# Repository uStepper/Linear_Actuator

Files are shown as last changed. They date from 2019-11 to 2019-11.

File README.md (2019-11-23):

# Linear_Actuator
This repository contains the files for the uStepper Linear Actuator - both M8 and T8x8 version. 
See more here: https://ustepper.com/store/kits/43-80-ustepper-linear-actuator.html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

<br /><span xmlns:dct="http://purl.org/dc/terms/" property="dct:title">uStepper & uStepper Linear Actuator</span> by <a xmlns:cc="http://creativecommons.org/ns#" href="www.ustepper.com" property="cc:attributionName" rel="cc:attributionURL">ON Development</a> is licensed under a <a rel="license" href="http://creativecommons.org/licenses/by-nc-sa/4.0/">Creative Commons Attribution-NonCommercial-ShareAlike 4.0 International License</a>.

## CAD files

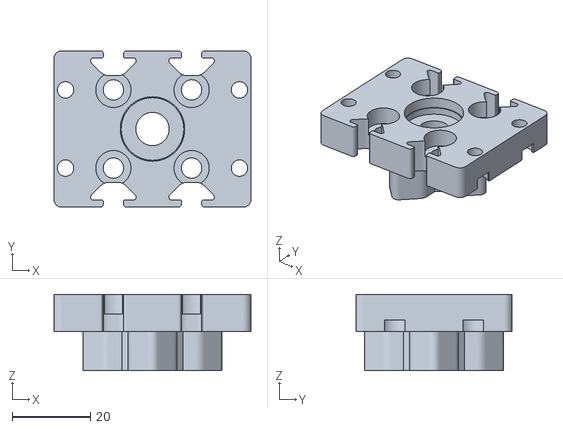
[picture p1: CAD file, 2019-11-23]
M8/STL/2-Bearingcap.stl
50.4 x 40.0 x 19.5

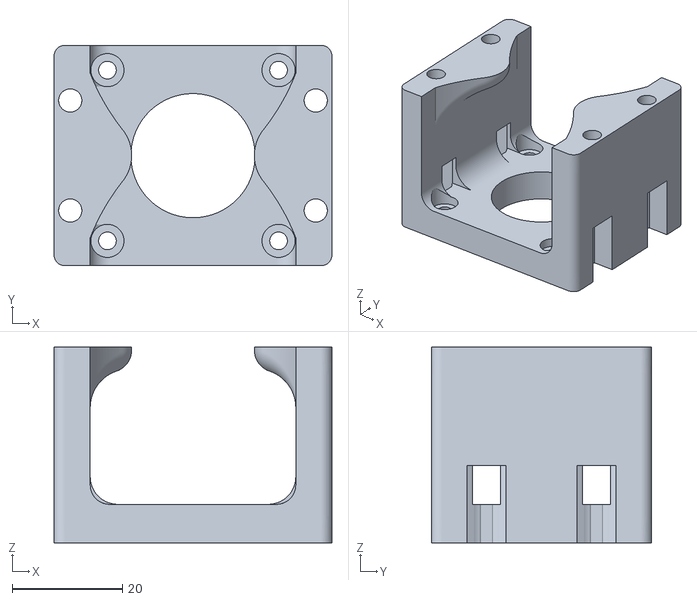
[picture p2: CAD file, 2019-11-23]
T8x8/STL/3-Motor_bracket.stl
50.4 x 40.0 x 35.5

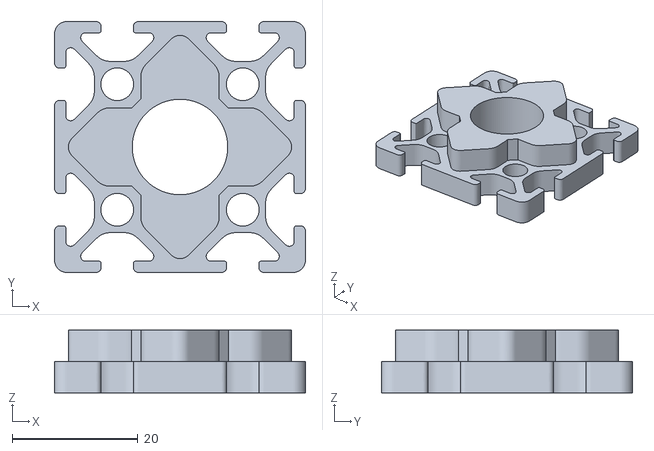
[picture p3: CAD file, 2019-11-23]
M8/STL/4-Endcap.stl
40.0 x 40.0 x 10.0

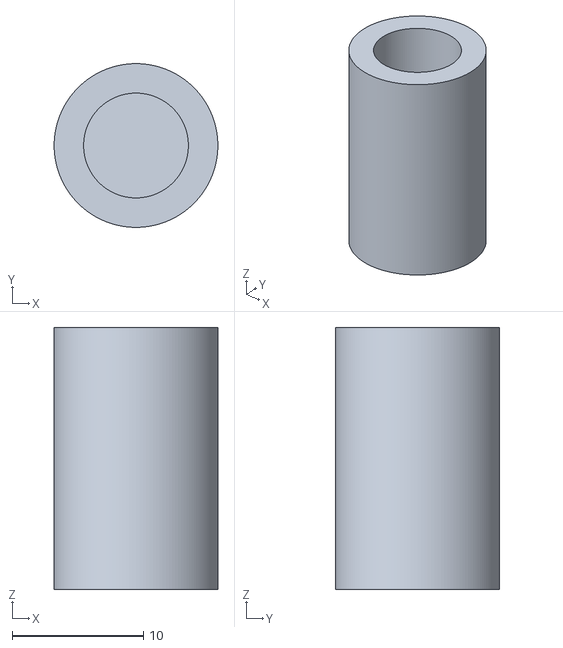
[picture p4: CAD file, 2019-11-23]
T8x8/STL/5-Rod_endcap.stl
12.5 x 12.5 x 20.0

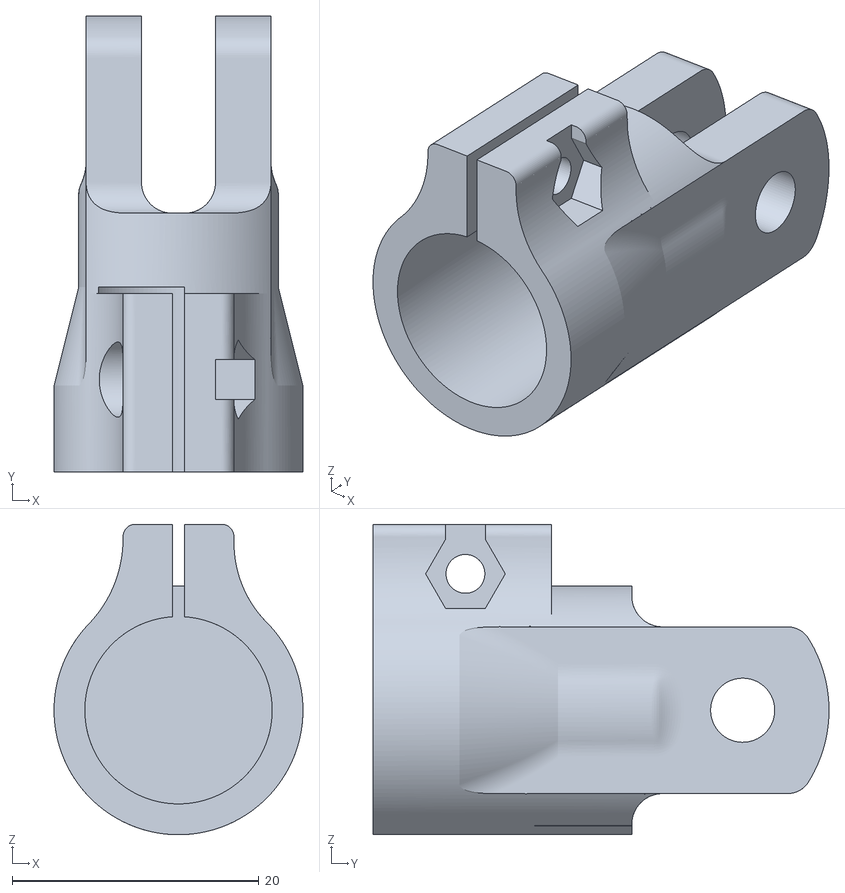
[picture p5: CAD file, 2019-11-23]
M8/STL/6-Rod_end.stl
20.2 x 37.0 x 25.2

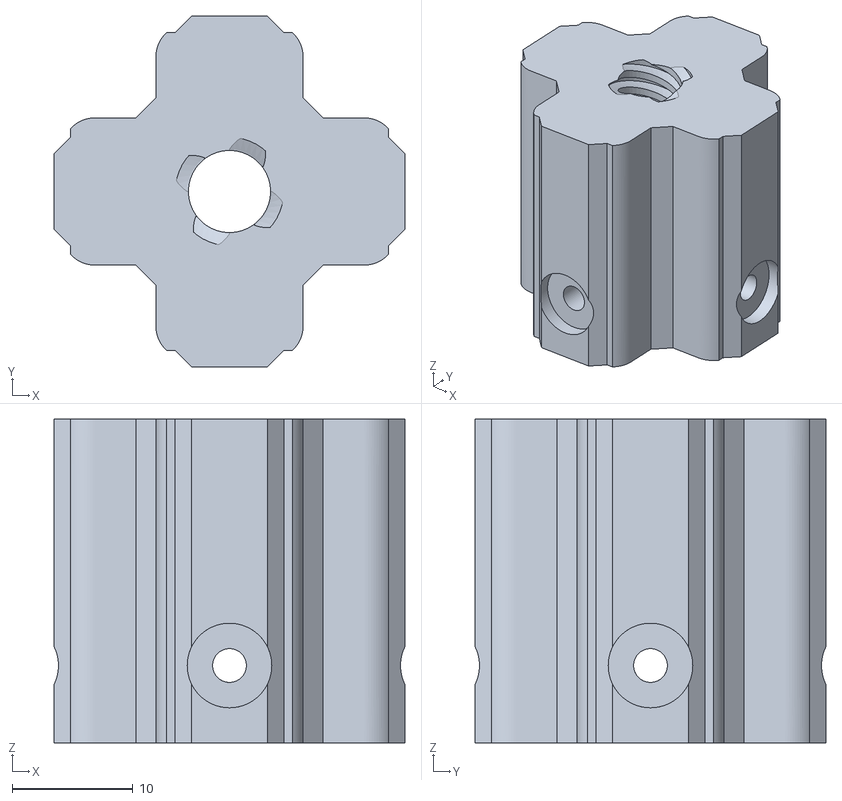
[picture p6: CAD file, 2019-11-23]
T8x8/STL/1-T8_nut.stl
29.1 x 29.1 x 26.8

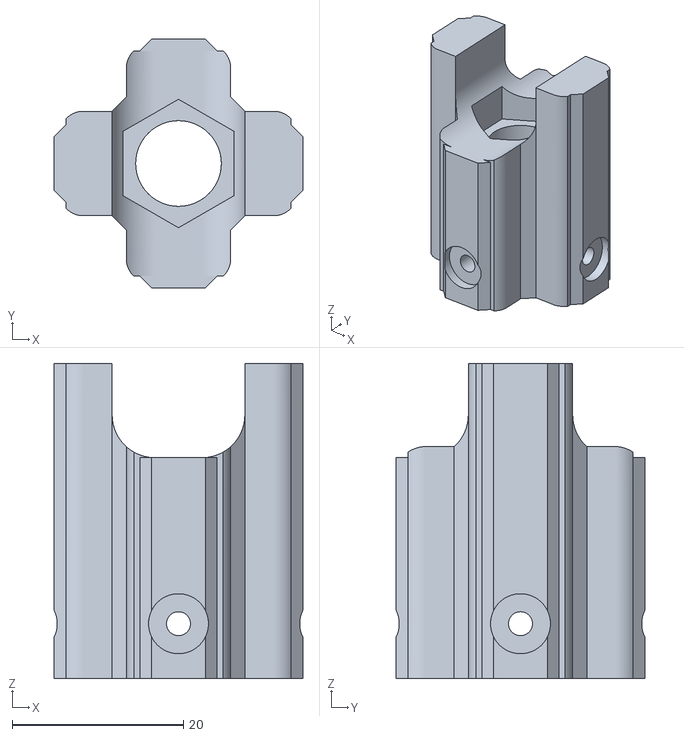
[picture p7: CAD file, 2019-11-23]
M8/STL/1-M8_nut.stl
29.1 x 29.1 x 36.8

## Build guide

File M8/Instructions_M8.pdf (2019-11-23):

# uStepper Linear Actuator

## M8 lead screw

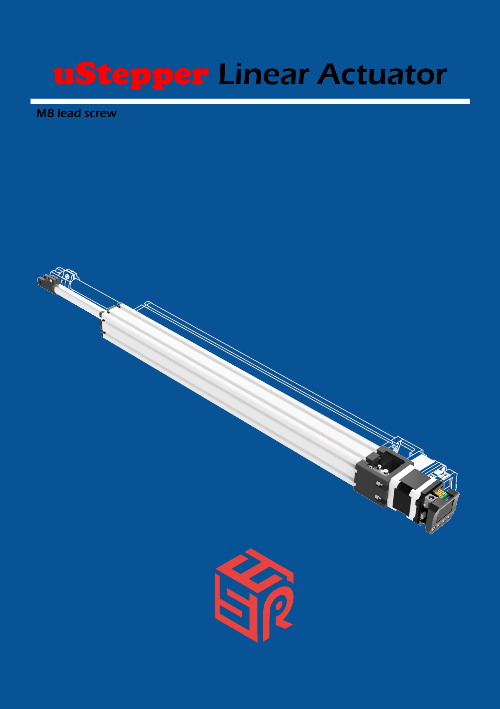
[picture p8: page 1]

# Introduction

## This document describes the assembly and use of uStepper Linear Actuator

and related products.

# Product: uStepper Linear Actuator M8

## Document revision: 1.0

## Author: MGN

## Approved by: THO

## Approval date: November 19th 2019

1

### 1 x

2

### 1 x

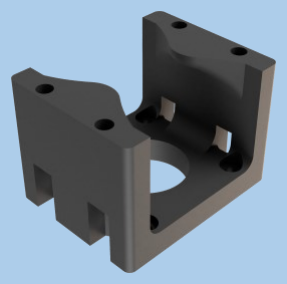
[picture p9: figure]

3

### 1 x

4

### 1 x

5

### 1 x

# Bill Of Materials

6

### 1 x

### 4 x M4 x 35 mm

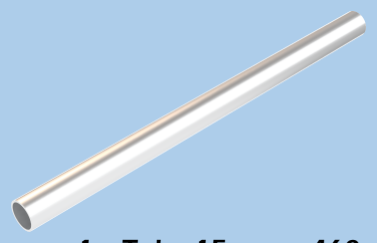
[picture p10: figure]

### 1 x Tube 15 mm x 460 mm

### 8 x M5 x 20 mm

### 2 x M8 nut

### 4 x M4 SL nut

### 1 x M8 SL nut

### 2 x F8-16M Bearing

# Bill Of Materials

### 3 x M3 x 10 mm

### 1 x M3 SL nut

### 1 x M8 lead screw x 470 mm

### 1 x 40x40 I-type slot 5, 450 mm

### 4 x 3.5x8 mm screw

### 1 x M8x5 coupler

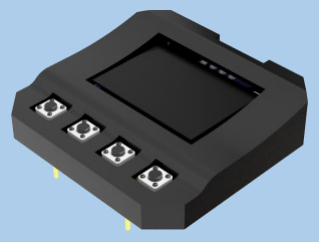
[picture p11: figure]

### 1 x uStepper Ego Shield S

### 1 x uStepper S w. motor

### 4 x M3 x 6 mm

# Linear Actuator Assembly

1x | 1x | 2x

1

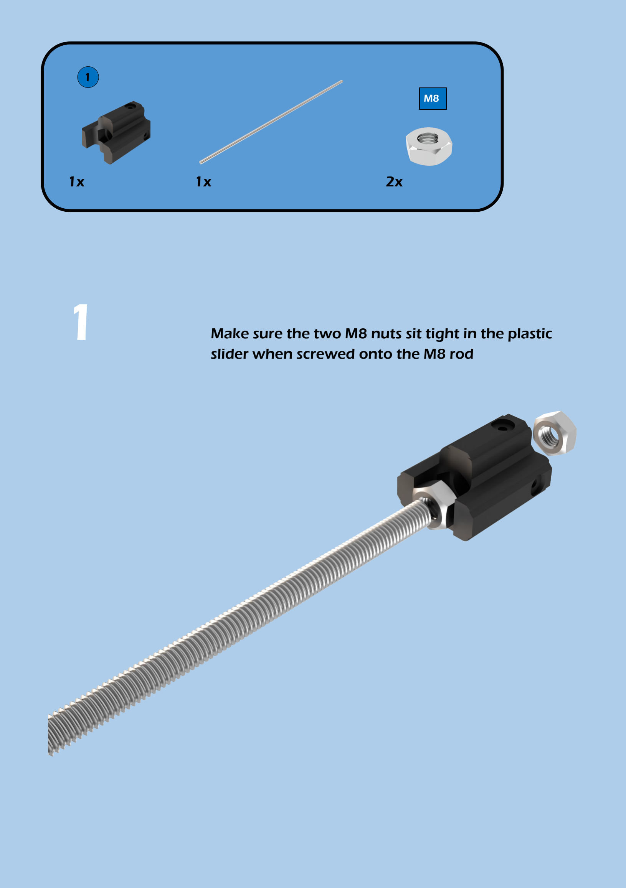
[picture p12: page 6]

1

M8

## Make sure the two M8 nuts sit tight in the plastic slider when screwed onto the M8 rod

1x | 2x | 1x | 4x | 1x

2

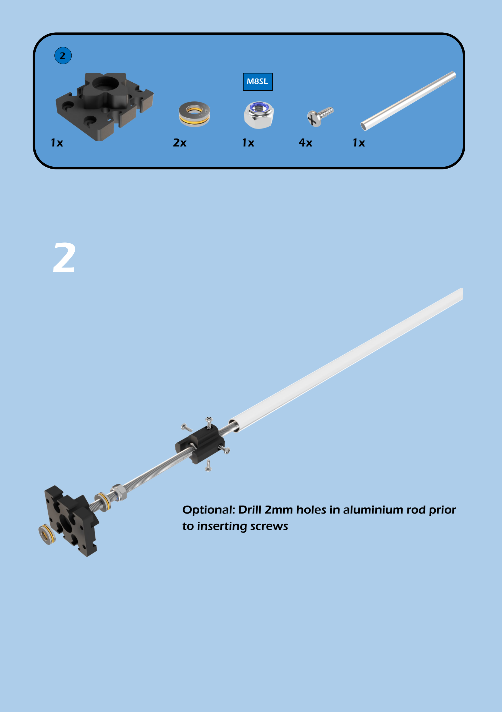
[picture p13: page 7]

2

M8SL

## Optional: Drill 2mm holes in aluminium rod prior to inserting screws

3

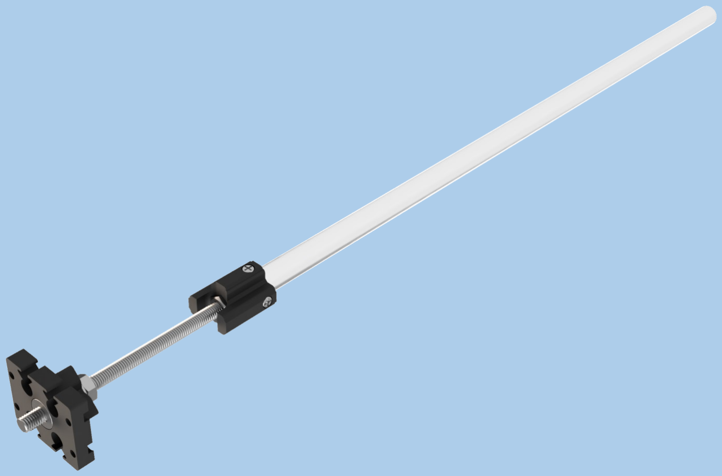
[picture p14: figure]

1x

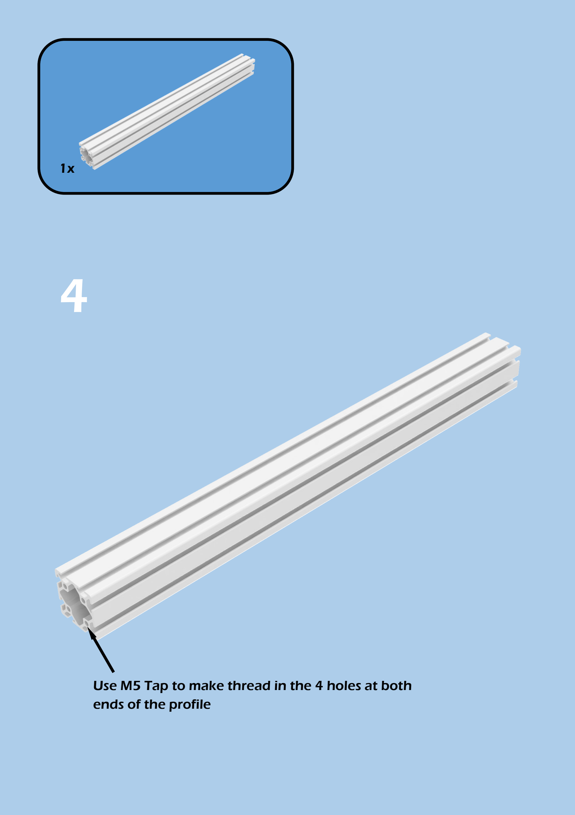
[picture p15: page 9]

4

## Use M5 Tap to make thread in the 4 holes at both ends of the profile

5

M5x20

4x

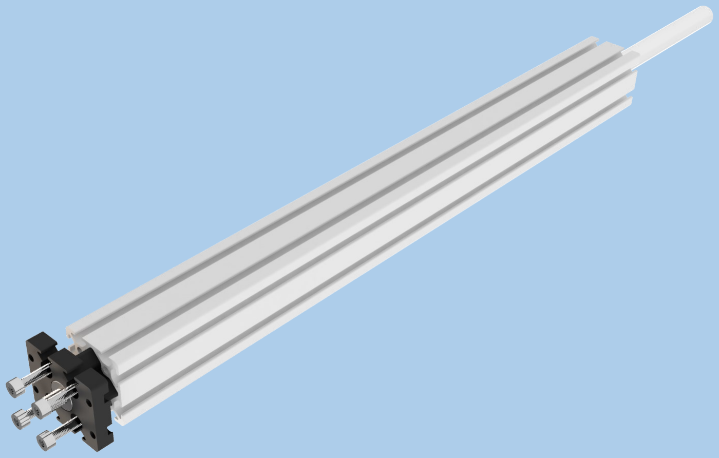
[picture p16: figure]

6

1x | 4x

M3x6

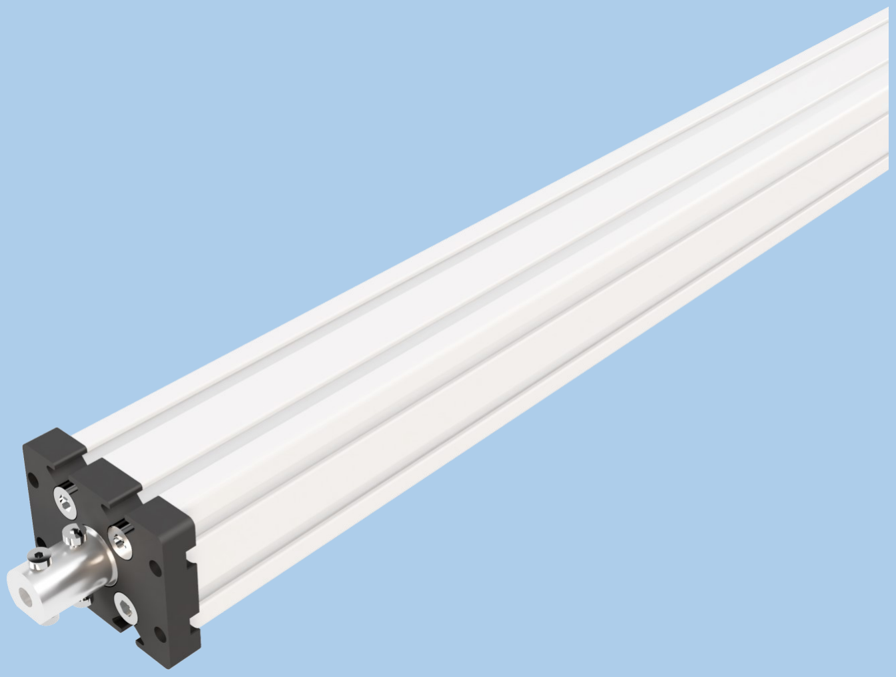
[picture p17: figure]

1x | 1x

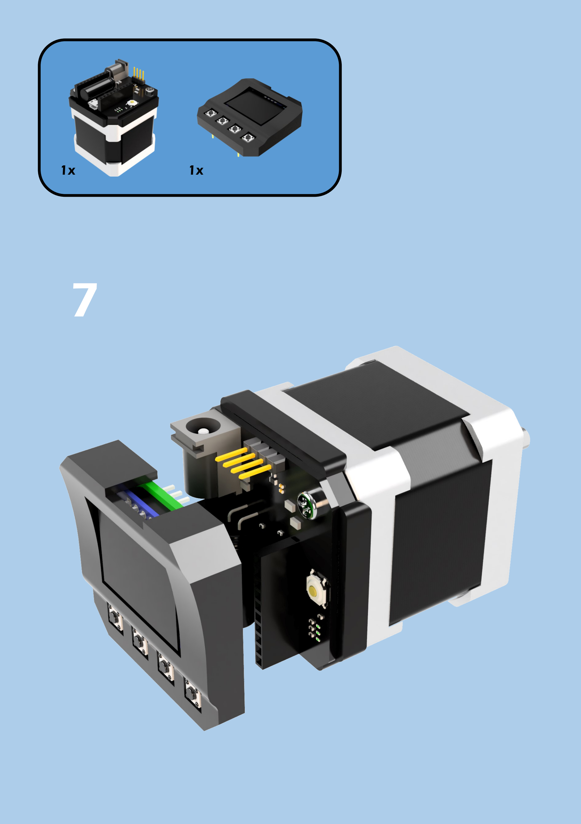
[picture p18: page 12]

7

1x | 2x

3

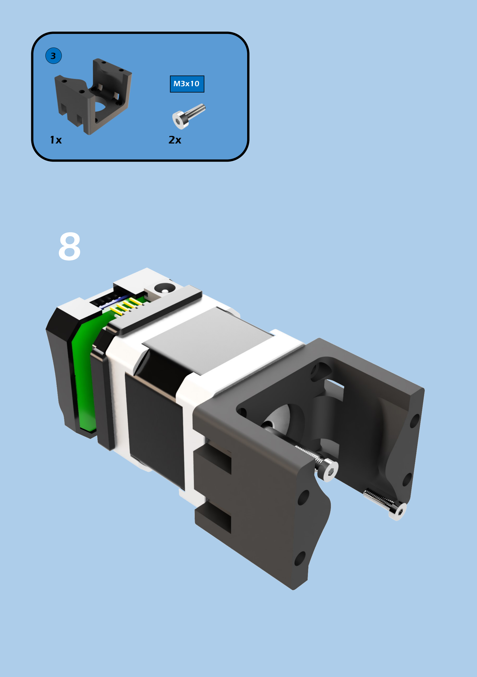
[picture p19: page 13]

8

M3x10

9

4x | 4x
M4x35 | M4SL

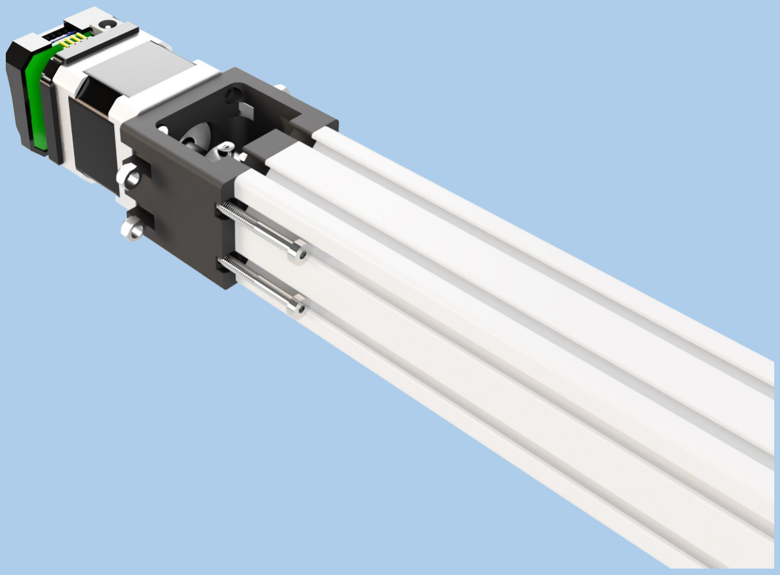
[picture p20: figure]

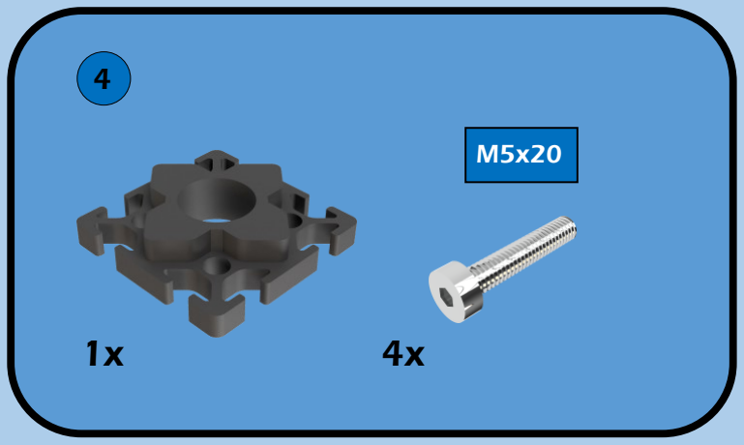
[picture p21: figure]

10

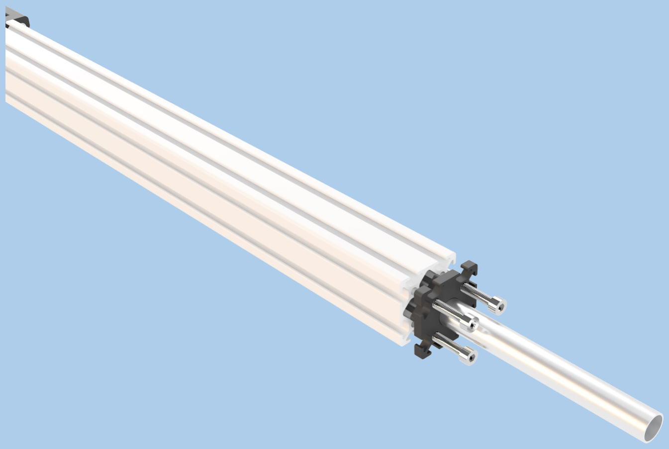
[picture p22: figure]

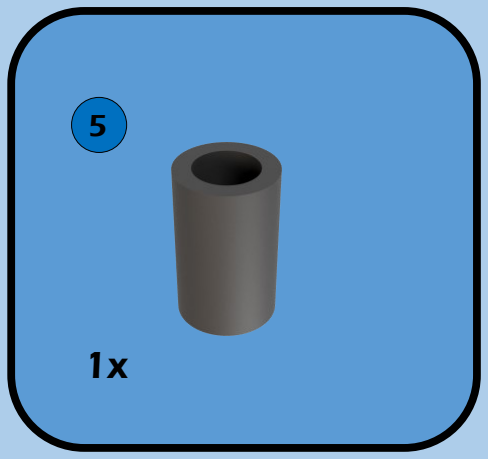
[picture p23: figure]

11

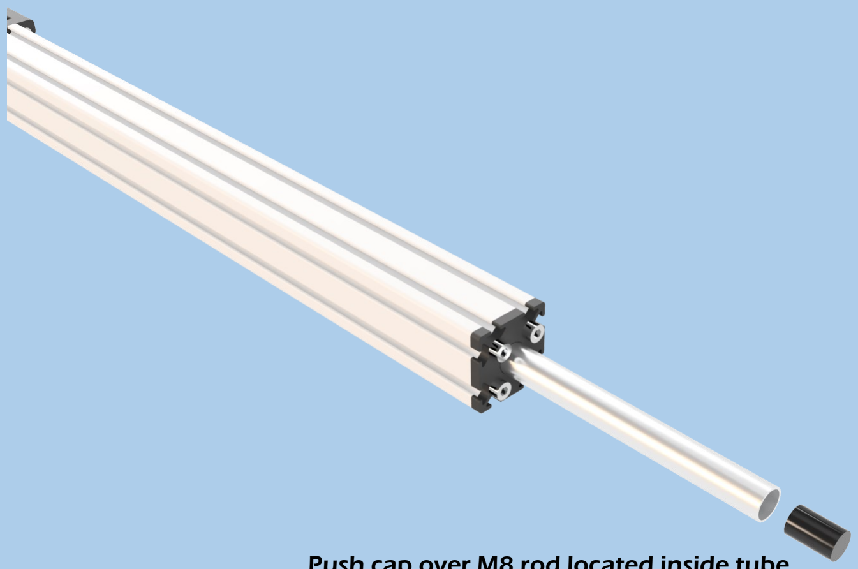
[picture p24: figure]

## Push cap over M8 rod located inside tube

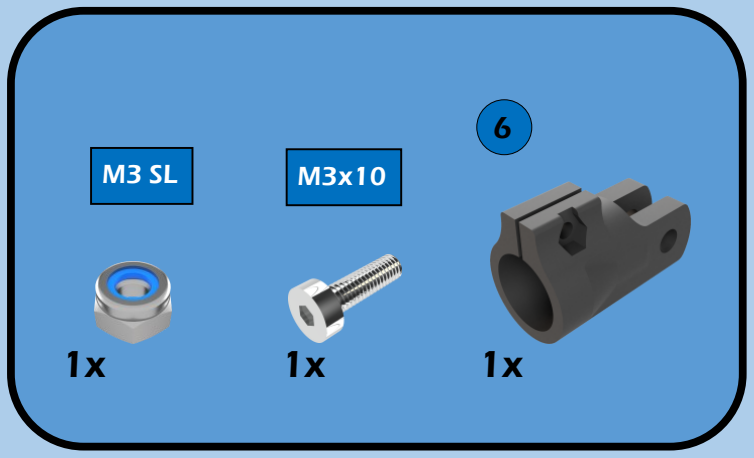
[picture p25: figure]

12

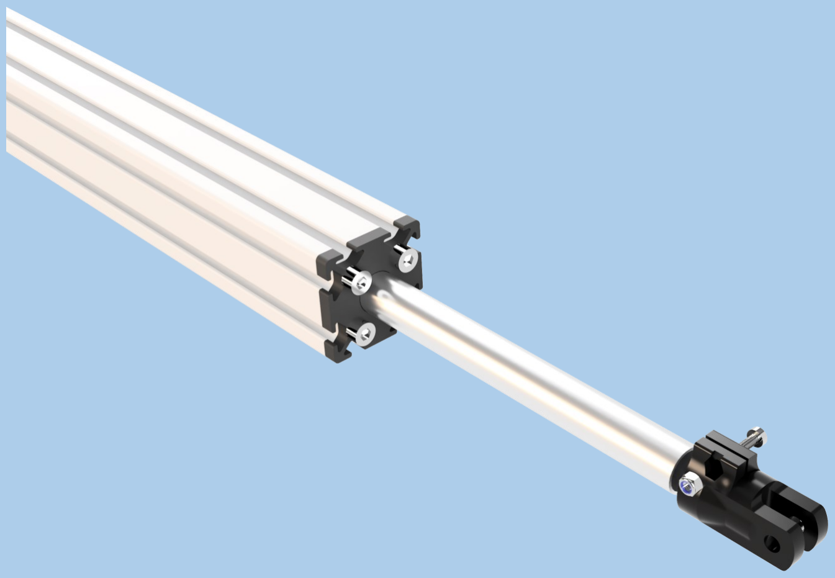
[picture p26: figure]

13

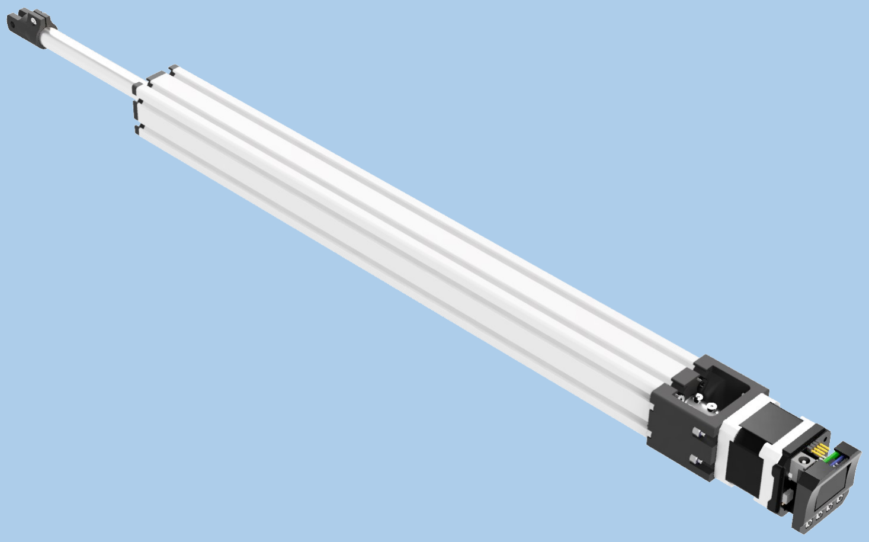
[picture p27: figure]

# Using uStepper & Ego Shield

To get started with using the linear actuator with uStepper S and Ego Shield S load the Ego Shield Teach

### example sketch and/or follow the instructions below !

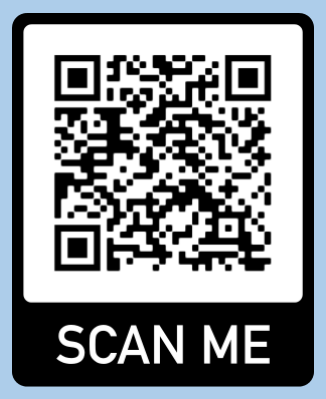
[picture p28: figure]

## Mounting uStepper

### To see how you mount uStepper S to your stepper motor correctly, please visit the

product sheet by pressing THIS LINK (https://ustepper.com/store/index.php?controller=attachment&id_attachment=9) or scanning the QR code here on the right !

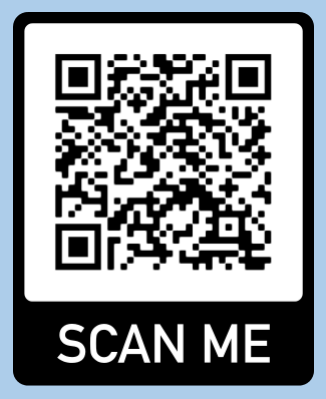
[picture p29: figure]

## Mounting and using Ego Shield

### To see how you mount the Ego Shield and what functionality comes with it please

visit the product sheet on THIS LINK (https://ustepper.com/store/index.php?controller=attachment&id_attachment=14) or scan the QR coder here on the right !

## Video Tutorials

On our YouTube channel you will find video tutorials on how to mount uStepper S, setting it up in the Arduino IDE and programming it. You will also find a tutorial for using the Ego Shield with the linear

### actuator !

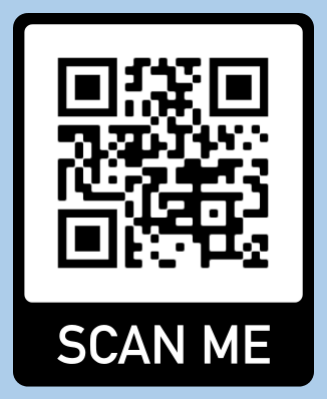
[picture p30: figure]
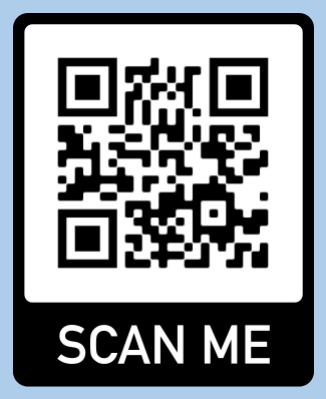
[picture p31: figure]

Mounting uStepper S (https://youtu.be/oYFnBv0kocI) | Programming uStepper S (https://youtu.be/V5M66Nhyn5s) | Using Ego Shield (https://youtu.be/wa8sdel2Xgg)

### For further info visit www.uStepper.com and our YouTube channel !

# Disclaimer

1 Disclaimers and Limitation of Liability

1.1 uStepper ApS and/or ON Development IVS (or any individuals affiliated with either of the two companies) can not be held responsible for any damage inflicted upon mounting or interfacing with uStepper products This also includes damage to stepper motors (both electrical and mechanical) or any other 3rd party hardware connected to or interfacing with any uStepper products. Most stepper motor cases are made of aluminum, and care must be taken when preparing the mountings for uStepper.

1.2 uStepper ApS and/or ON Development IVS (or any individuals affiliated with either of the two companies) can not be held responsible for any damage inflicted upon assembly of the uStepper Robot Arm. This includes damage to 3D printed parts, which must be considered to be of prototyping quality compared to injection moulded parts. Care must be taken while assembling 3D printed parts, and use of excessive force may lead to damage of the parts.

1.3 By using the uStepper products (including, but not limited to, hardware and software) you acknowledge that uStepper ApS and/or ON Development IVS (or any individuals affiliated with either of the two companies) can not be held responsible for any personal injuries and/or damage to any 3rd party hardware that may occur when using the uStepper products.

1.4 To the extent permitted by law, uStepper ApS and/or ON Development IVS will not be liable for any indirect or consequential loss or damage, of any kind, (including without limitation loss of business, opportunity, data, profits) arising out of or in connection with the use of any products (including, but not limited to, hardware and software), developed, produced or sold by uStepper ApS and/or ON Development IVS (or any individuals affiliated with either of the two companies).

1.5 Nothing in these Terms and Conditions shall be construed so as to hold uStepper ApS and/or ON Development IVS liable for death or personal injury as a result of the negligence of uStepper ApS and/or ON Development IVS or that of its employees or agents.

2 Indemnity

2.1 You agree to indemnify and hold uStepper ApS and/or ON Development IVS and its employees and agents harmless from and against all liabilities, legal fees, damages, losses, costs and other expenses in relation to any claims or actions brought against uStepper ApS and/or ON Development IVS arising out of any breach by you of these Terms and Conditions or other liabilities arising out of your use of this Website.

2.2 You agree to indemnify and hold uStepper ApS and/or ON Development IVS and its employees and agents harmless from and against all liabilities, legal fees, damages, losses, costs and other expenses in relation to any claims or actions brought against uStepper ApS and/or ON Development IVS arising out of any breach by you of these Terms and Conditions or other liabilities arising out of your use of products(including, but not limited to, hardware and software) developed, produced or sold by uStepper ApS and/or ON Development IVS (or any individuals affiliated with either of the two companies).

3 Severance

If any of these Terms and Conditions should be determined to be invalid, illegal or unenforceable for any reason by any court of competent jurisdiction then such Term or Condition shall be severed and the remaining Terms and Conditions shall survive and remain in full force and effect and continue to be binding and enforceable.

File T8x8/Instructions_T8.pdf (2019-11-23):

# uStepper Linear Actuator

## T8 lead screw

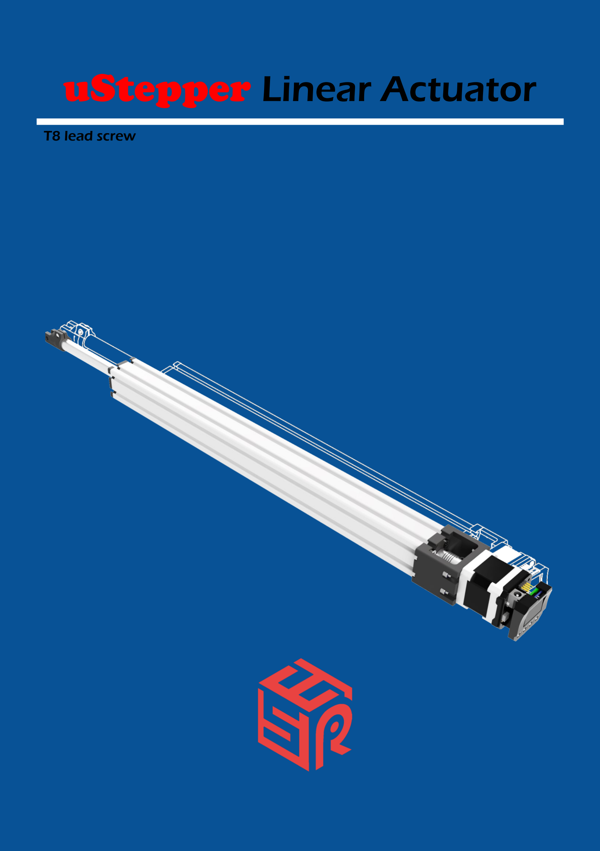
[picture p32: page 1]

# Introduction

## This document describes the assembly and use of uStepper Linear Actuator

and related products.

# Product: uStepper Linear Actuator T8

## Document revision: 1.0

## Author: MGN

## Approved by: THO

## Approval date: November 19th 2019

1

### 1 x

2

### 1 x


3

### 1 x

4

### 1 x

5

### 1 x

# Bill Of Materials

6

### 1 x

### 4 x M4 x 35 mm


### 1 x Tube 15 mm x 460 mm

### 8 x M5 x 20 mm

### 4 x M4 SL nut

### 1 x 8mm collar

### 2 x F8-16M Bearing

# Bill Of Materials

### 3 x M3 x 10 mm

### 1 x M3 SL nut

### 1 x T8x8 lead screw 500 mm

### 1 x 40x40 I-type slot 5, 450 mm

### 4 x 3.5x8 mm screw

### 1 x M8x5 coupler


### 1 x uStepper Ego Shield S

### 1 x uStepper S w. motor

### 2 x M8 washer

# Linear Actuator Assembly

1x | 1x

1

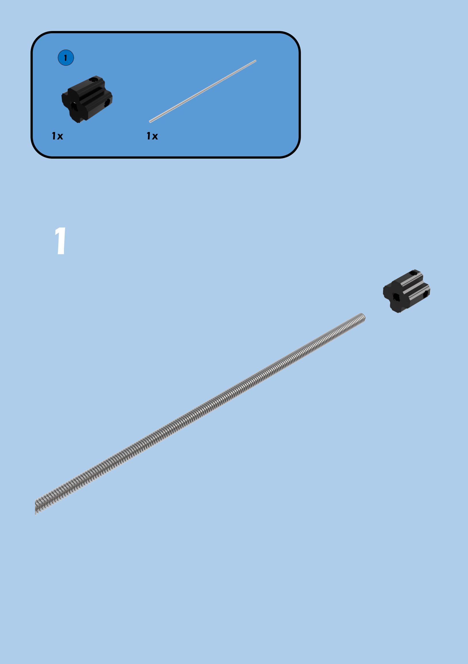
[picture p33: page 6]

1

1x | 2x | 2x | 4x | 1x

2

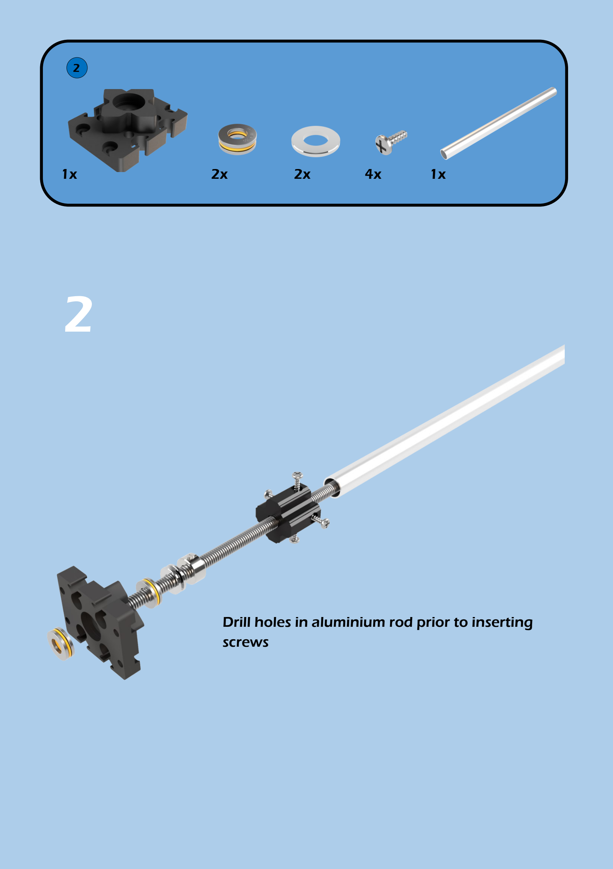
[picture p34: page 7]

2

## Drill holes in aluminium rod prior to inserting screws

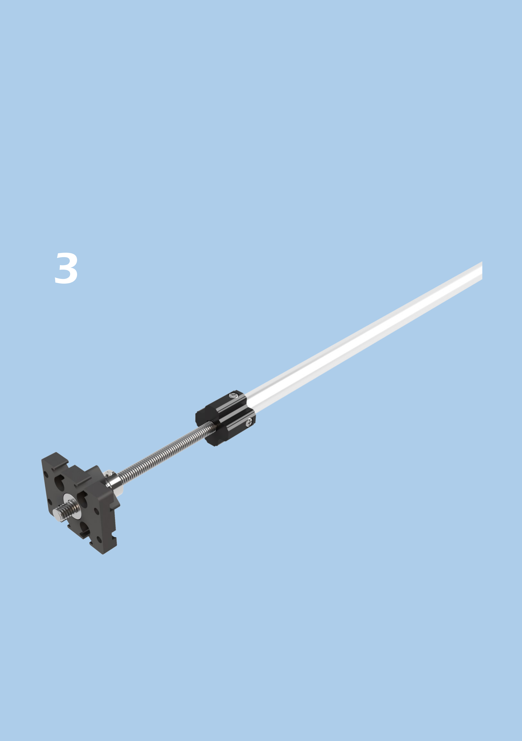
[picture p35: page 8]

3

1x


4

## Use M5 Tap to make thread in the 4 holes at both ends of the profile

5

M5x20

4x

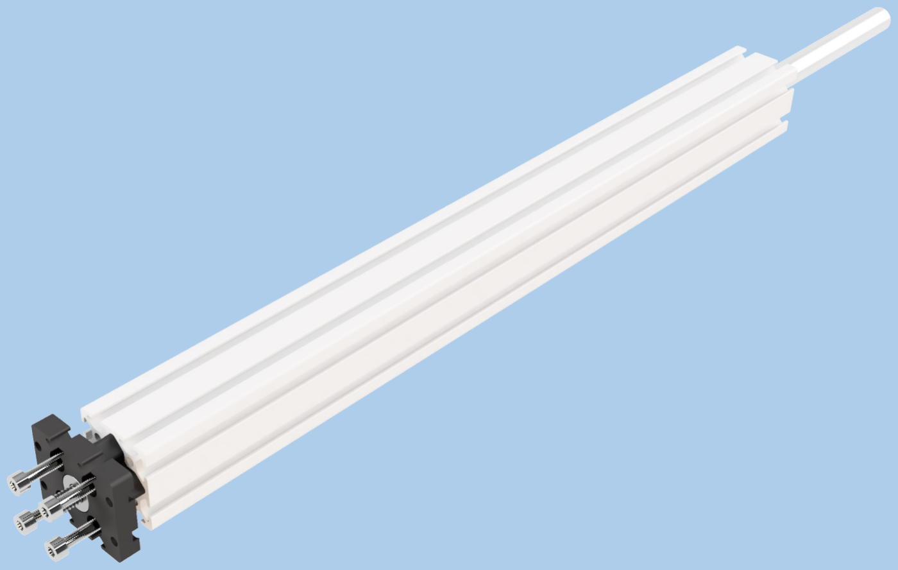
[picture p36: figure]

6

1x

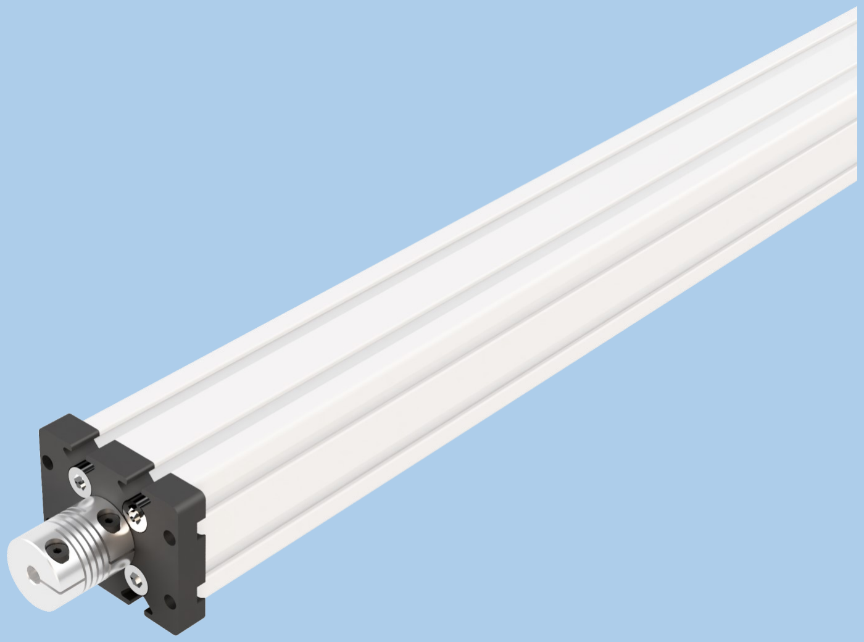
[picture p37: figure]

1x | 1x


7

1x | 2x

4

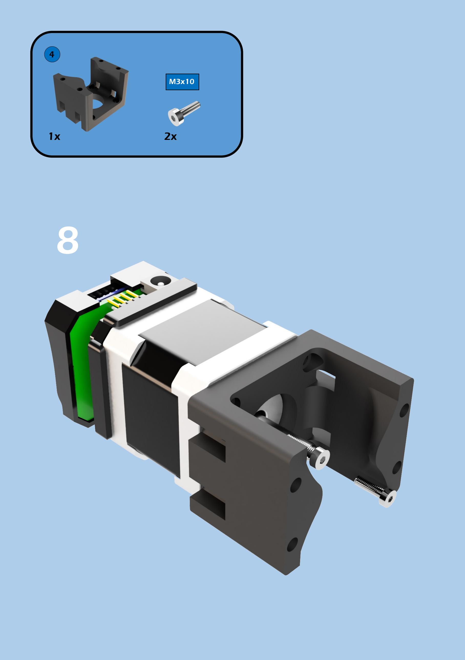
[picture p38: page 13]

8

M3x10

9

4x | 4x
M4x35 | M4SL

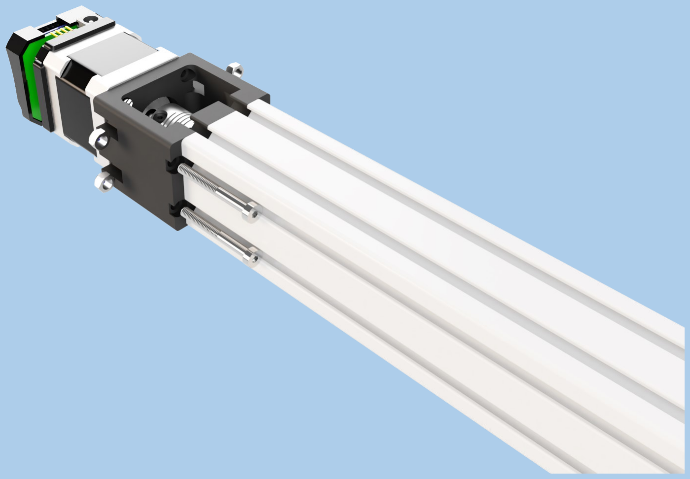
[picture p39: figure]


10



11

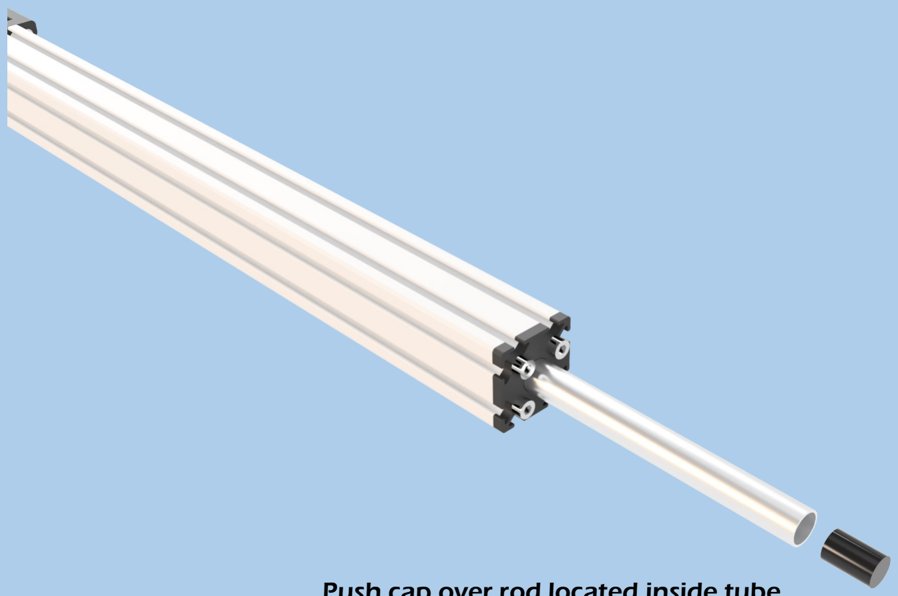
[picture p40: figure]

## Push cap over rod located inside tube


12


13

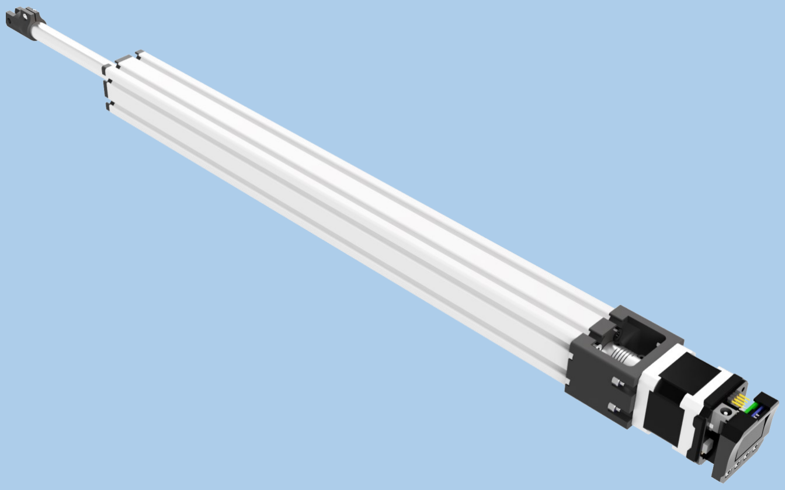
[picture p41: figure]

# Using uStepper & Ego Shield

To get started with using the linear actuator with uStepper S and Ego Shield S load the Ego Shield Teach

### example sketch and/or follow the instructions below !


## Mounting uStepper

### To see how you mount uStepper S to your stepper motor correctly, please visit the

product sheet by pressing THIS LINK (https://ustepper.com/store/index.php?controller=attachment&id_attachment=9) or scanning the QR code here on the right !


## Mounting and using Ego Shield

### To see how you mount the Ego Shield and what functionality comes with it please

visit the product sheet on THIS LINK (https://ustepper.com/store/index.php?controller=attachment&id_attachment=14) or scan the QR coder here on the right !

## Video Tutorials

On our YouTube channel you will find video tutorials on how to mount uStepper S, setting it up in the Arduino IDE and programming it. You will also find a tutorial for using the Ego Shield with the linear

### actuator !


Mounting uStepper S (https://youtu.be/oYFnBv0kocI) | Programming uStepper S (https://youtu.be/V5M66Nhyn5s) | Using Ego Shield (https://youtu.be/wa8sdel2Xgg)

### For further info visit www.uStepper.com and our YouTube channel !

# Disclaimer

1 Disclaimers and Limitation of Liability

1.1 uStepper ApS and/or ON Development IVS (or any individuals affiliated with either of the two companies) can not be held responsible for any damage inflicted upon mounting or interfacing with uStepper products This also includes damage to stepper motors (both electrical and mechanical) or any other 3rd party hardware connected to or interfacing with any uStepper products. Most stepper motor cases are made of aluminum, and care must be taken when preparing the mountings for uStepper.

1.2 uStepper ApS and/or ON Development IVS (or any individuals affiliated with either of the two companies) can not be held responsible for any damage inflicted upon assembly of the uStepper Robot Arm. This includes damage to 3D printed parts, which must be considered to be of prototyping quality compared to injection moulded parts. Care must be taken while assembling 3D printed parts, and use of excessive force may lead to damage of the parts.

1.3 By using the uStepper products (including, but not limited to, hardware and software) you acknowledge that uStepper ApS and/or ON Development IVS (or any individuals affiliated with either of the two companies) can not be held responsible for any personal injuries and/or damage to any 3rd party hardware that may occur when using the uStepper products.

1.4 To the extent permitted by law, uStepper ApS and/or ON Development IVS will not be liable for any indirect or consequential loss or damage, of any kind, (including without limitation loss of business, opportunity, data, profits) arising out of or in connection with the use of any products (including, but not limited to, hardware and software), developed, produced or sold by uStepper ApS and/or ON Development IVS (or any individuals affiliated with either of the two companies).

1.5 Nothing in these Terms and Conditions shall be construed so as to hold uStepper ApS and/or ON Development IVS liable for death or personal injury as a result of the negligence of uStepper ApS and/or ON Development IVS or that of its employees or agents.

2 Indemnity

2.1 You agree to indemnify and hold uStepper ApS and/or ON Development IVS and its employees and agents harmless from and against all liabilities, legal fees, damages, losses, costs and other expenses in relation to any claims or actions brought against uStepper ApS and/or ON Development IVS arising out of any breach by you of these Terms and Conditions or other liabilities arising out of your use of this Website.

2.2 You agree to indemnify and hold uStepper ApS and/or ON Development IVS and its employees and agents harmless from and against all liabilities, legal fees, damages, losses, costs and other expenses in relation to any claims or actions brought against uStepper ApS and/or ON Development IVS arising out of any breach by you of these Terms and Conditions or other liabilities arising out of your use of products(including, but not limited to, hardware and software) developed, produced or sold by uStepper ApS and/or ON Development IVS (or any individuals affiliated with either of the two companies).

3 Severance

If any of these Terms and Conditions should be determined to be invalid, illegal or unenforceable for any reason by any court of competent jurisdiction then such Term or Condition shall be severed and the remaining Terms and Conditions shall survive and remain in full force and effect and continue to be binding and enforceable.
